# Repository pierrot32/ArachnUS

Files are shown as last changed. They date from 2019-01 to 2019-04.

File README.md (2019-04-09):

# ArachnUS
Projet de conception d'un robot araignée à 3 pattes.

## Mécanique du robot:
Fichier RobotCAD contient toutes les informations pour imprimer ou modifier les pièces du robot avec le logiciel Solidworks.
Plus d'informations sont données dans le fichier.

## Carte openCR
Voir le dossier Code/OpenCr pour la procédure d'installation et d'utilisation de code du robot

## Autres Cartes 
### Utilisation de la carte PCA9685 (branchements sur la carte openCr)
Voir le dossier Documentation électronique

### Uilisation du capteur de distance
Voir le dossier Documentation électronique

## Interface:
Voir le dossier Code/python pour la procédure d'installation et d'utilisation de l'interface pour le contrôle du robot.

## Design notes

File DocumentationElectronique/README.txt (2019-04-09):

Ici sont réunies les premier codes de tests et les informations sur le hardware que nous avons utilisé.

Ci-dessous une liste de références pour l'électronique du robot:

Guide d'utilisation du contrôleur PCA9685:
https://learn.adafruit.com/16-channel-pwm-servo-driver/overview

Guide d'utilisateur de la carte OpenCR:
http://emanual.robotis.com/docs/en/parts/controller/opencr10/
http://support.robotis.com/en/product/controller/opencr.htm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

Fiches techniques :
Moteur MG996R : http://magicduino.com/Images/ItemsMedia/File/7203.pdf
Capteur de hauteur HC-SR04 :
La section utile au capteur est le chapitre 24 du tutoriel, c'est dans cette section que le code utilisé a été pris.
Cette section contient aussi les informations sur l'alimentation électrique du capteur.
https://github.com/Freenove/Freenove_Ultimate_Starter_Kit_for_Arduino/blob/master/Tutorial.pdf

Pour l'installation de la carte OpenCR sur arduinoIDE (sur Windows): 
1) Fichier -> préférence -> URL de gestionnaire des cartes suppl. -> https://raw.githubusercontent.com/ROBOTIS-GIT/OpenCR/master/arduino/opencr_release/package_opencr_index.json
2) Tools -> board -> board manager -> "opencr" dans la barre de recherche -> install
3) Tools -> board -> "OpenCR Board"
4) Tools -> port -> COMX (*une fois connecte)

Pour MAC ou autre, voir le guide d'utilisateur de la carte OpenCR^^

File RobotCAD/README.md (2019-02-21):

# RobotCAD
Ce fichier contient tous les dessins 3D pour construire le robot, ainsi que les informations pour le fabriquer

## Pieces à imprimer:
Fichier contenant les fichier STL et STEP des pieces à imprimer. Voir le README de ce fichier pour avoir les quantitées exact de pièces à imprimer

## Base/Pattes:
Pieces SLDPRT utilisées pour concevoir le robot

## Assemblage:
Assemblages du robot et document sur comment assembler le robot.

## Cartes/ServoMoteurs:
Dessins 3D des cartes et des servo moteurs du robot

## Dev:
Fichier contenant les pièces de développement utilisés dans la conception du robot

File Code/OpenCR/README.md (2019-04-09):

##  Guide d'utilisateur de la carte OpenCR:
http://emanual.robotis.com/docs/en/parts/controller/opencr10/
http://support.robotis.com/en/product/controller/opencr.htm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

## OpenCR et PCA9685:
Pour utiliser la carte OpenCR dans notre appliquation, il faut:
1. Télécharger arduinoIDE
2. Télécharger la carte "OpenCR" dans arduinoIDE 
  a) Fichier -> préférence -> URL de gestionnaire des cartes suppl. -> https://raw.githubusercontent.com/ROBOTIS-GIT/OpenCR/master/arduino/opencr_release/package_opencr_index.json
  b) Tools -> board -> board manager -> "opencr" dans la barre de recherche -> install
  c) Tools -> board -> "OpenCR Board"
  d) Tools -> port -> COMX (*une fois connecte)
3. Télécharger la librairie "adafruit servo" dans arduinoIDE
4. Assembler la carte PCA9685 (https://learn.adafruit.com/16-channel-pwm-servo-driver/assembly)
5. Faire les connections électriques entre le PCA9685, le OpenCR et les servos moteur (https://learn.adafruit.com/16-channel-pwm-servo-driver/hooking-it-up)
6. Connecter l'alimentation externe
7. Connecter la prise USB et téléverser le programme "Programme principal"

*NOTE*: Toujours brancher l'alimentation externe avant de brancher le cable USB

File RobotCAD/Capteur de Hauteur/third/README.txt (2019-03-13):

the source of the files contained in this directory is: https://grabcad.com/library/ultrasonic-distance-measuring-sensor-module-for-arduino-1

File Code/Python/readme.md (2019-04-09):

## Installation de python
1.  Télécharger python 3.7
2.  Télécharger Pycharm (ou autre environnement de programmation en python)
3.  Ajouter les librairies suivantes: pip (19.0.1), numpy (1.16.1), pyserial (3.4) et matplotlib (3.0.3)

## Ajustement du code pour utilisation de la communication en l'ordinateur et la carte oprenCR
1.  Veuillez vérifier que le code utilise le bon port USB de votre ordinateur ('COM3')
    a)  Ouvrir arduinoIDE
    b)  Brancher la carte openCR
    c)  Outil(barre de menu) -> port -> Noter le port
2. Ajuster le code de communication
  a)  Ouvrir le fichier communication.py à l'aide de pycharm
  b)  Voir ligne 119
  c)  Changer COM3 par le port utilisé par votre ordinateur
    
##  Utilisation de l'interface
1.  Ouvrir le fichier Main.py
2.  S'assurer que la carte openCR est branché sur l'ordinateur
3.  Exécuter le code
4.  Le robot démarre en mode arrêt
5.  Changer le mode à manuel pour le contrôle individuel de chaque moteur
6.  ...

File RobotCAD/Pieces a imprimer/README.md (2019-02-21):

# Pieces à imprimer:

Voici la liste des pieces à imprimer et leur quantitée

Barre_Bleu1           -> x3

Barre_Bleu2           -> x3

Barre_Bleu3           -> x3

Barre_Rouge1          -> x3
 
Barre_Rouge2          -> x3
 
Barre_Rouge3          -> x3
 
Barre_Vert            -> x3
 
Base_Moteur           -> x3
 
Espaceur_Plaques      -> x4
 
Joint_RB              -> x3
 
Pied_de_patte         -> x3
 
Plaque_Bas            -> x1
 
Plaque_Top            -> x1
 
Porteur_moteur        -> x2

Protecteur_de_Cartes  -> x1
 
Support_de_Cartes     -> x1

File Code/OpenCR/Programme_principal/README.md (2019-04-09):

## Utilisation du programme de contrôle du robot
  Pour utiliser ce programme, il faut préalablement avoir réaliser les étapes pour avoir accès à l'interface.
  
  1. Ouvir le programme principal
  2. Téléverser le programme vers la carte openCR
  3. Lancer l'interface
  4. Utiliser l'interface pour contrôler les différents modes du robot

## Ajustement du range des pattes du robots
  
  1. Ouvrir le code fonctionsServos
  2. Faire monter le robot le plus haut possible à l'aide de l'interface
  3. Changer les ranges dans le code pour s'assurer de respecter les limites de la pattes

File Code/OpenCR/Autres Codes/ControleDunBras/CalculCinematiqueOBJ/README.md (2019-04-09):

Ici a été développé la classe -> ObjCinematique.h

Une fois inclue dans un code elle, permet de faire la cinématique directe et inverse de notre systeme.

Cette classe utilise la librairie "matrix", concue par François Grondin,
dans laquel nous avons ajouté quelques fonctionnalités.

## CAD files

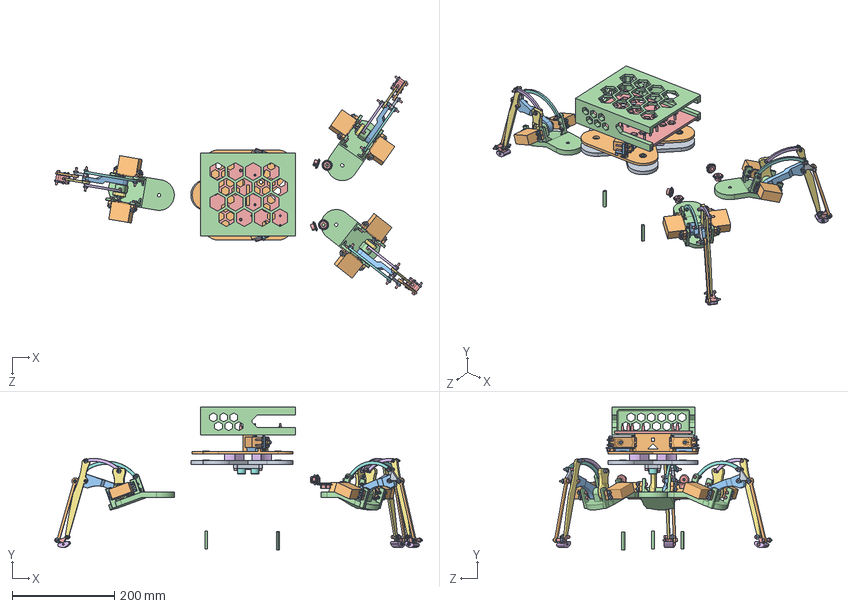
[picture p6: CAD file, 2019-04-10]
RobotCAD/Assemblages/Tripod.SLDASM
720.4 x 279.4 x 428.7 mm
Plaque_Bas
Plaque_Top
Porteur_moteur x 2
Protecteur_de_Cartes
Support_de_Cartes
Espaceur_Plaques x 4
bearing_2 x 6
hc-sr04
Support_Capteur
servo x 8
shaft x 8
Washer_plas x 16
socket head cap screw_ai x 64
Barre_Bleu2 x 3
Barre_Bleu3 x 3
Barre_Rouge1 x 3
Barre_Rouge2 x 3
Barre_Rouge3 x 3
Barre_Vert x 3
Base_moteurs x 3
Joint_RB x 3
Pied_de_patte x 3
Barre_Bleu1 x 3
Washer_1 x 30
bearing_1 x 6
Spacer pour servo moteur_1 x 24
machine screw nut hex_ai x 56
Shaft_1 x 3
615398.STEP x 4
632134_91375A436.STEP x 4

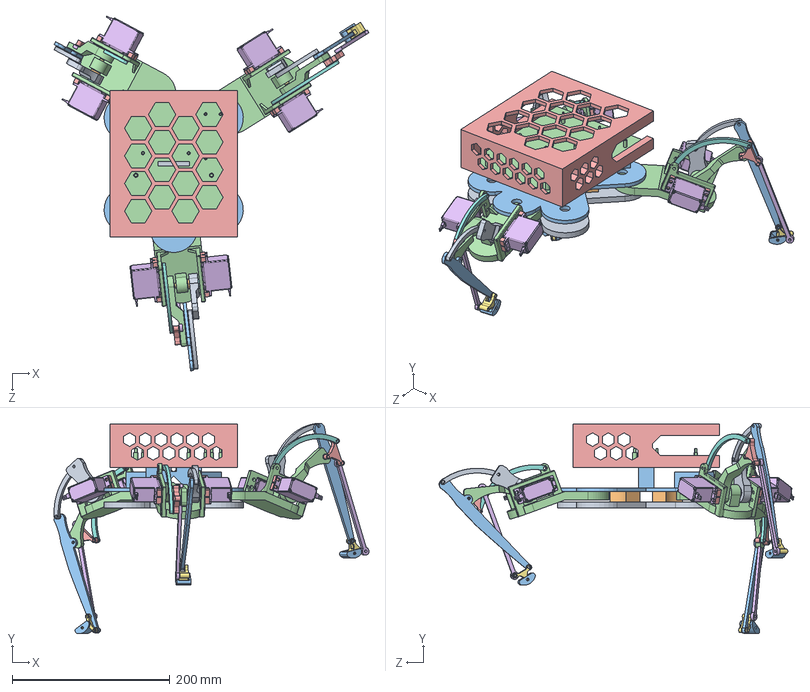
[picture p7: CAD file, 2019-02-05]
RobotCAD/Dev/Assemblage_du_robot.SLDASM
399.4 x 266.8 x 449.9 mm
base_v3-bas
SpacerCarteDuBas x 4
base_v3-top
Base x 3
Spacer pour servo moteur x 24
hs-422_sws x 6
shaft-18 x 3
Connecteur_servo_moteur x 6
Bleu1 x 3
bearing x 6
Bleu3 x 3
Vert x 3
Rouge2 x 3
Rouge3 x 3
Joint R-B x 3
Rouge1 x 3
Bleu2.0 x 3
WASHER x 36
Pied de patte x 3
support_carte
cover carte

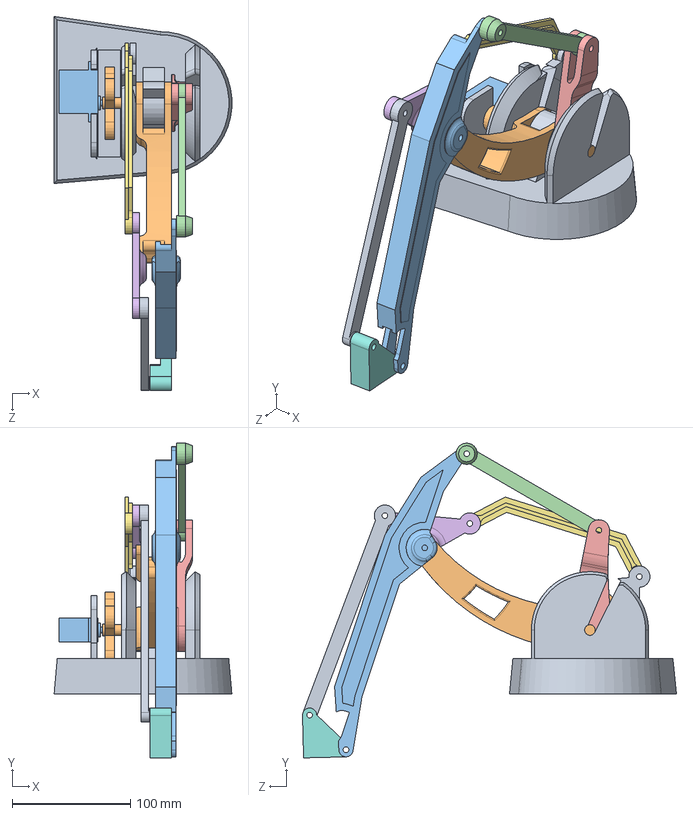
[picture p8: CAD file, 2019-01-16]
RobotCAD/Dev/Robot_fait_pour_projet_S1/Robotic Arm/Robotic.SLDASM
150.1 x 265.8 x 315.7 mm
Boutte_Servo
Modèle_servomoteur

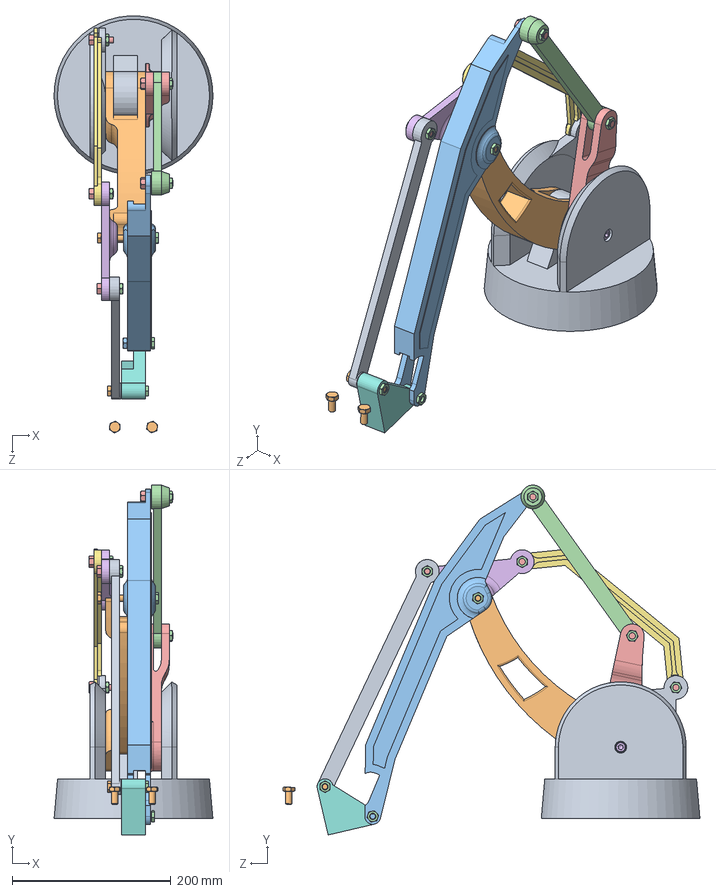
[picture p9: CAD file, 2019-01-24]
RobotCAD/Dev/Robot_ordinaire_download/Robotic Arm/Robotic.SLDASM
199.9 x 440.4 x 524.8 mm
hex cap screw_am x 4
formed hex screw_am
hex nut jam_am x 9
hex screw_am x 5
socket head cap screw_am

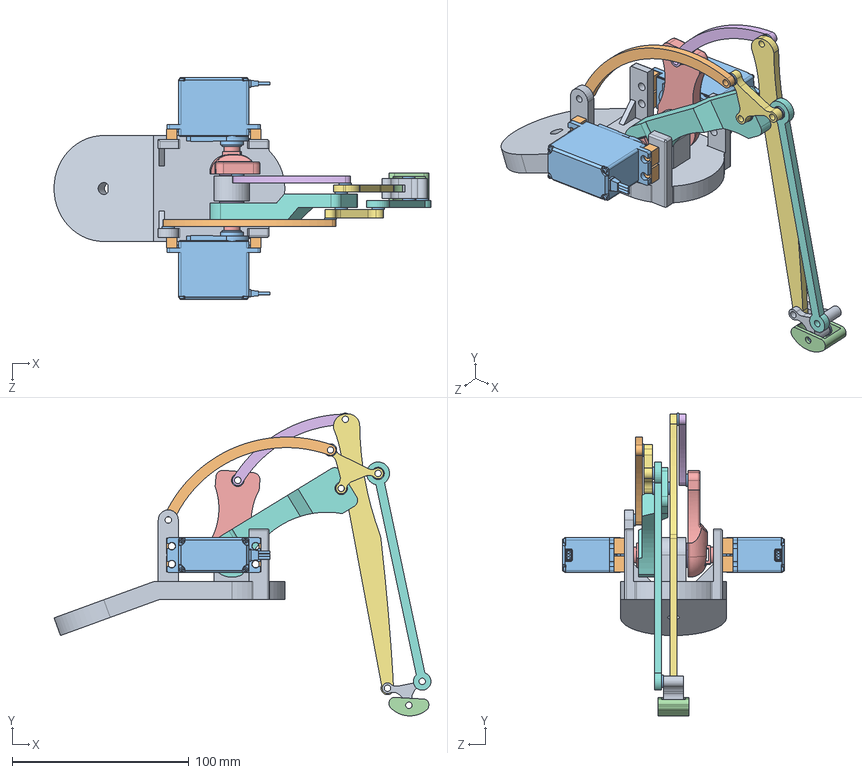
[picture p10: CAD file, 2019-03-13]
RobotCAD/Dev/Robot_v1_POL/Assemblage1.SLDASM
213.4 x 171.4 x 125.6 mm
Base2
Spacer pour servo moteur x 8
hs-422_sws x 2
shaft-18
Connecteur_servo_moteur x 2
bearing x 2
Bleu3
Vert
Joint R-B
Rouge1
WASHER x 10
Pied de patte
Bleu1
Bleu2.0
Rouge2
Rouge3

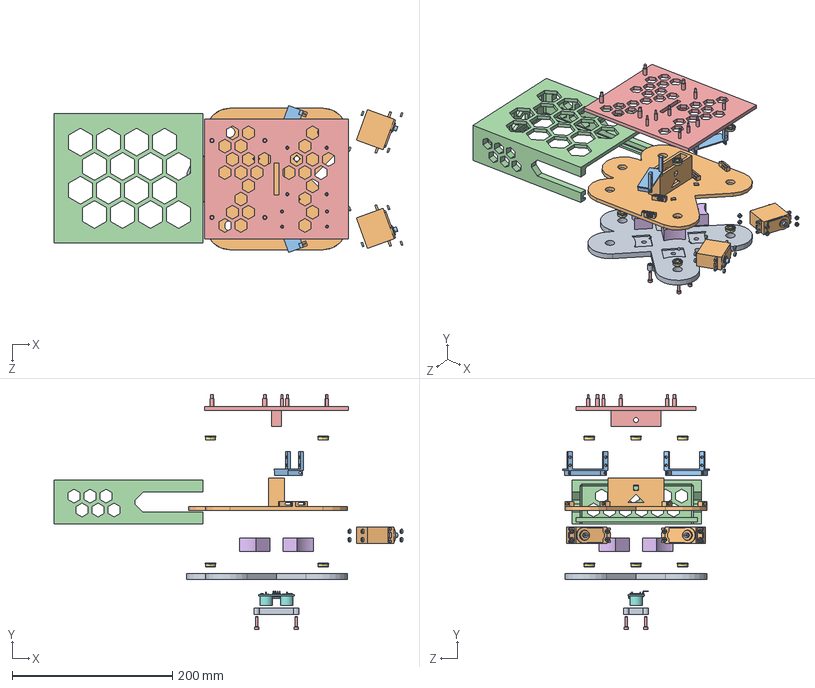
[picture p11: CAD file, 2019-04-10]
RobotCAD/Assemblages/Base.SLDASM
435.4 x 293.5 x 183.2 mm
Plaque_Bas
Plaque_Top
Porteur_moteur x 2
Protecteur_de_Cartes
Support_de_Cartes
Espaceur_Plaques x 4
bearing_2 x 6
hc-sr04
Support_Capteur
servo x 2
shaft x 2
Washer_plas x 16
socket head cap screw_ai x 4

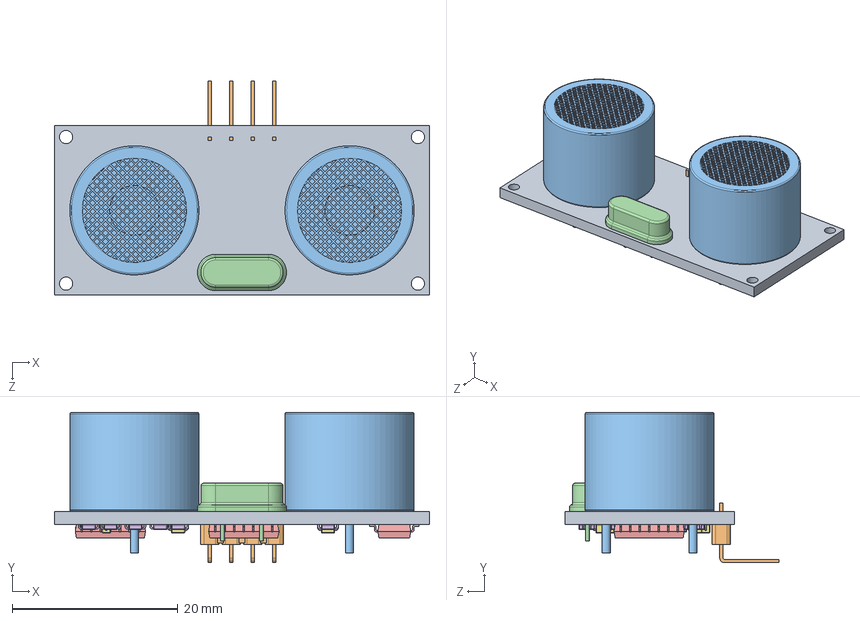
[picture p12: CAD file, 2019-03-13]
RobotCAD/Capteur de Hauteur/hc-sr04.SLDASM
45.3 x 18.2 x 25.9 mm
pcb
connector
speaker x 2
osilator
microprocessor_1 x 3
resistor x 14
Capacitor x 7

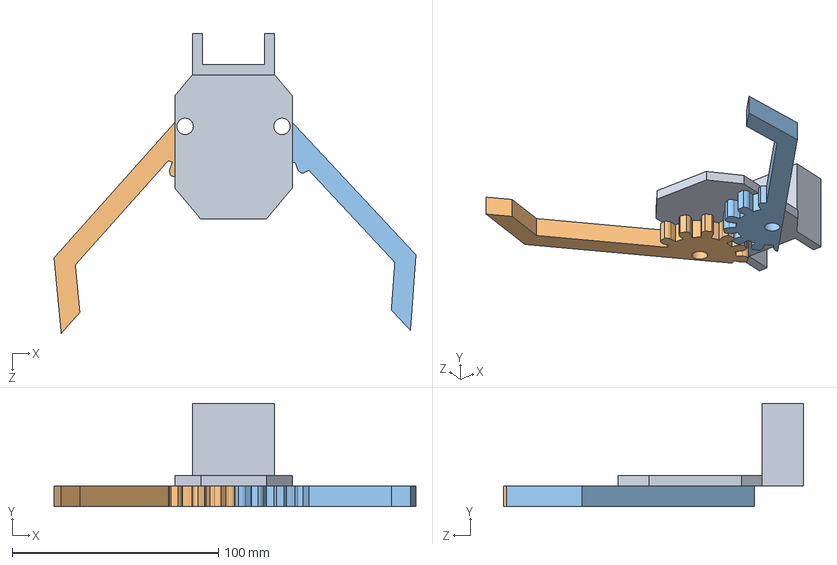
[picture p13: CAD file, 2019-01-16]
RobotCAD/Dev/Robot_fait_pour_projet_S1/Robotic Arm/Assem2.SLDASM
175.7 x 50.0 x 145.5 mm

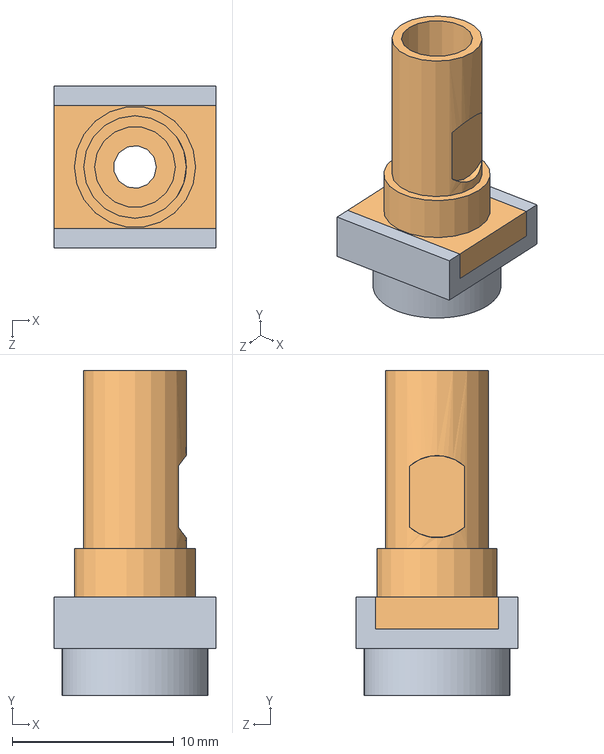
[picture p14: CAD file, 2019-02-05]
RobotCAD/ServoMoteur/connecteur_servo_engr_assemble.SLDASM
10.0 x 20.1 x 10.0 mm
Connecteur_servo_moteur
connecteur_servo_engrenage

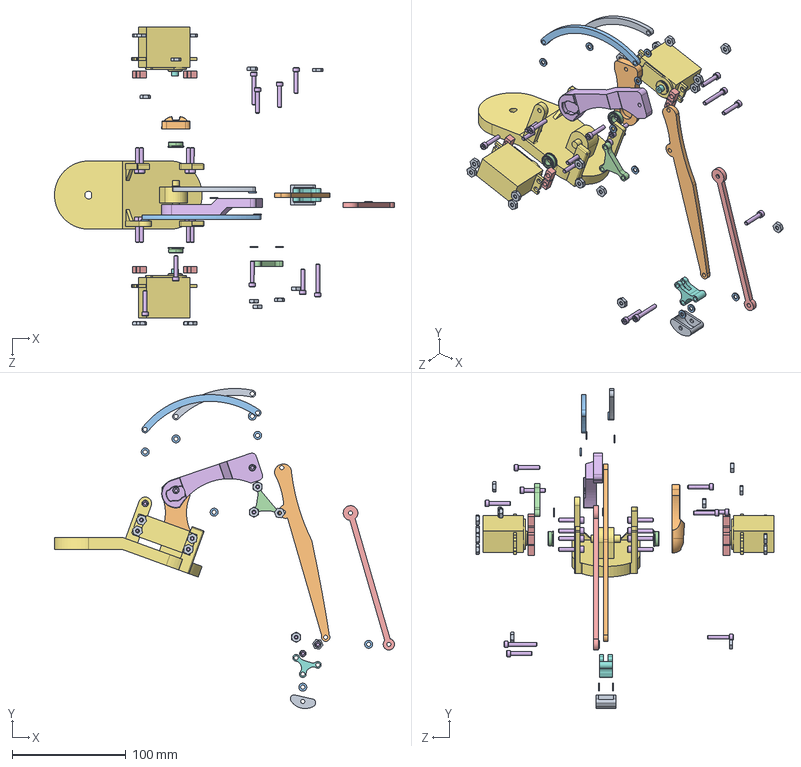
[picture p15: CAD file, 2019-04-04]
RobotCAD/Assemblages/Patte.SLDASM
299.1 x 281.5 x 262.0 mm
Barre_Bleu2
Barre_Bleu3
Barre_Rouge1
Barre_Rouge2
Barre_Rouge3
Barre_Vert
Base_moteurs
Joint_RB
Pied_de_patte
Barre_Bleu1
Washer_1 x 10
bearing_1 x 2
Spacer pour servo moteur_1 x 8
socket head cap screw_ai x 17
servo x 2
shaft x 2
machine screw nut hex_ai x 16

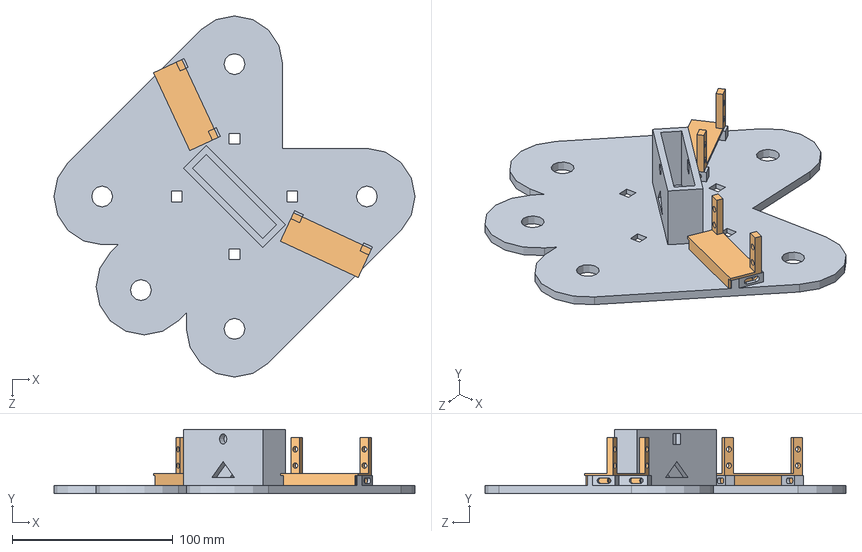
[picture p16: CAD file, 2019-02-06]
RobotCAD/Dev/base/assemblage_base_top_glissiere.SLDASM
224.9 x 40.0 x 224.9 mm
base_v3-top-glissiere
glissiere_connexion_moteur x 2

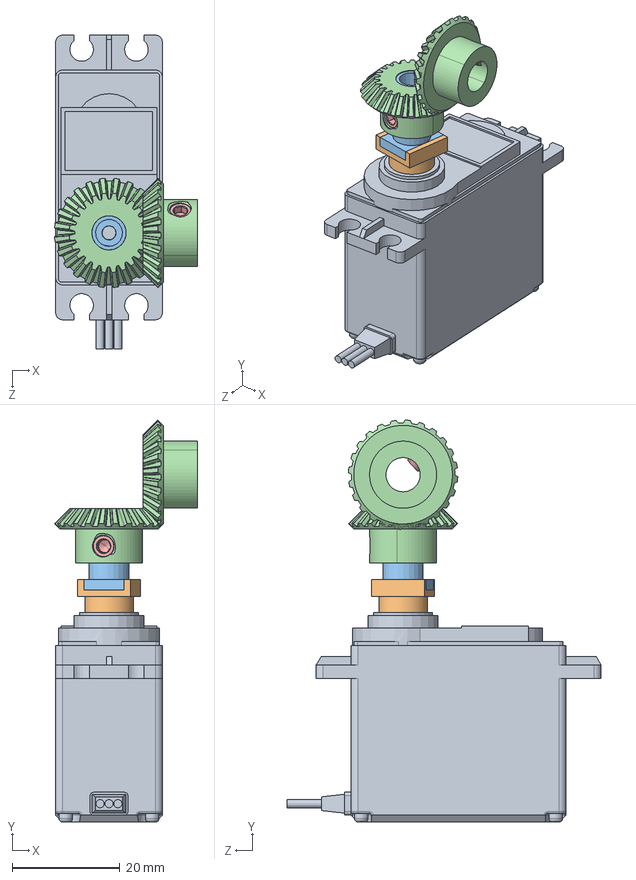
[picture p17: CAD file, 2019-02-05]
RobotCAD/ServoMoteur/assemblage_servo_engrenage.SLDASM
26.6 x 74.6 x 58.2 mm
hs-422_sws
Connecteur_servo_moteur
connecteur_servo_engrenage
615398.STEP x 2
632134_91375A436.STEP x 2

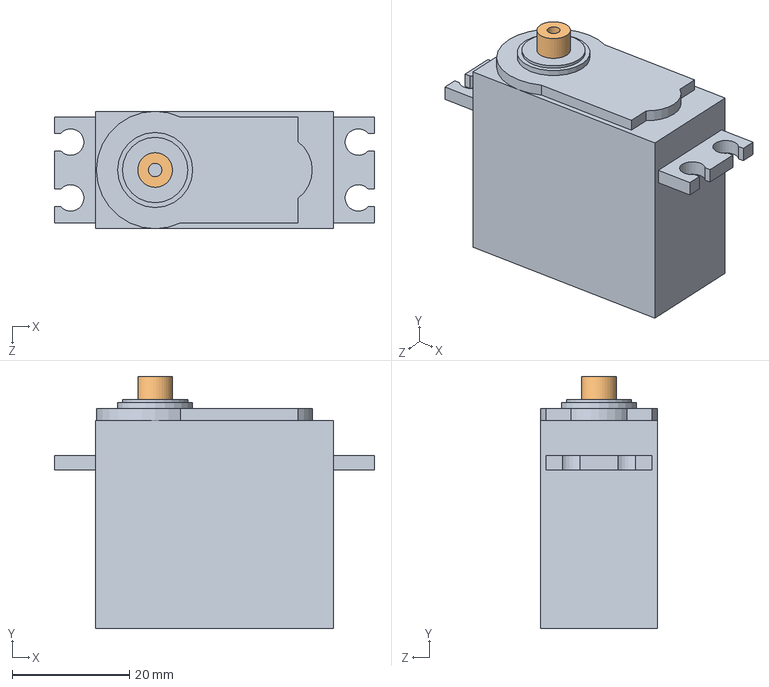
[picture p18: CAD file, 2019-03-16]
RobotCAD/ServoMoteur/MG996R/MG996R.SLDASM
54.5 x 43.0 x 20.0 mm
servo
shaft

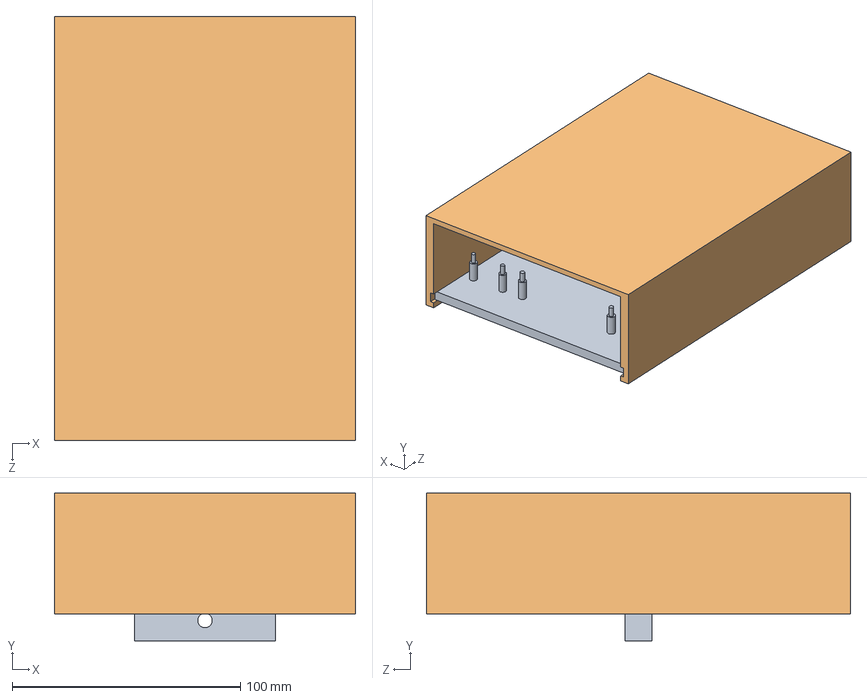
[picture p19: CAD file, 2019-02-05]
RobotCAD/Dev/base/assemblage_support_carte_et_cover.SLDASM
132.0 x 64.9 x 186.0 mm
support_carte
cover carte

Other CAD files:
RobotCAD/ServoMoteur/assemblage_servo_engrenage_2e_cote.SLDASM
RobotCAD/Dev/base/assemblage_base_support_carte.SLDASM
RobotCAD/Dev/base/assemblage_base_top.SLDASM
RobotCAD/base/Assemblage_de_la_base.SLDASM
RobotCAD/Assemblages/Patte.SLDDRW
RobotCAD/Base/Espaceur_Plaques.SLDPRT
RobotCAD/Base/Plaque_Bas.SLDPRT
RobotCAD/Base/Plaque_Top.SLDPRT
RobotCAD/Base/Porteur_moteur.SLDPRT
RobotCAD/Base/Protecteur_de_Cartes.SLDPRT
RobotCAD/Base/Support_de_Cartes.SLDPRT
RobotCAD/Capteur de Hauteur/Support_Capteur.SLDPRT
RobotCAD/Capteur de Hauteur/hc-sr04.SLDPRT
RobotCAD/Capteur de Hauteur/osilator.SLDPRT
RobotCAD/Capteur de Hauteur/pcb.SLDPRT
RobotCAD/Capteur de Hauteur/third/microprocessor_1.sldprt
RobotCAD/Capteur de Hauteur/third/resistor.sldprt
RobotCAD/Capteur de Hauteur/third/speaker.sldprt
RobotCAD/Cartes/16-channel-pca9685-1/PCA9685.SLDPRT
RobotCAD/Cartes/OpenC_dimensions.SLDPRT
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

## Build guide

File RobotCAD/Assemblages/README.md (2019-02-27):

# Arachnus
Projet de conception d'un robot araignée à 3 pattes.

## Assemblage

Pour assembler notre robot, il faut imprimer toutes les pièces nécessaires pour le robot qui sont dans le dossier "Pièces à imprimer" (https://github.com/pierrot32/ArachnUS/tree/master/RobotCAD/Pieces%20a%20imprimer).

Assembler chacune des pattes du robot en se basant sur le modèle 3D et en suivant ces recommendations :
1. Utiliser des boulons 6-32 3/4" pour assembler le robot, sauf pour la jonction entre les pièces bleu3, rouge2 et verte où un boulon de 1" est requis.
2. Utiliser des écrous autobloquant pour éviter qu'ils ne se desserrent durant l'utilisation du robot.
3. Placer une rondelle entre chaque pièce de plastique pour éviter le frottement plastique/plastique
4. Placer les moteurs en dernier et utiliser les séparateurs de caoutchouc pour qu'ils soient bien alligner avec l'arbre de rotation
5. S'assurer que chaque moteur peut atteindre les 2 maximums de leur axe de rotation

Assembler le robot en se basant sur le modèle 3D de l'assemblage complet et en suivant ces recommendations :
1. Utiliser des boulons 1/4-20 de 1 1/4"
2. Faire passer les câbles des différents moteurs dans la cavité centrale avant de placer le support à cartes

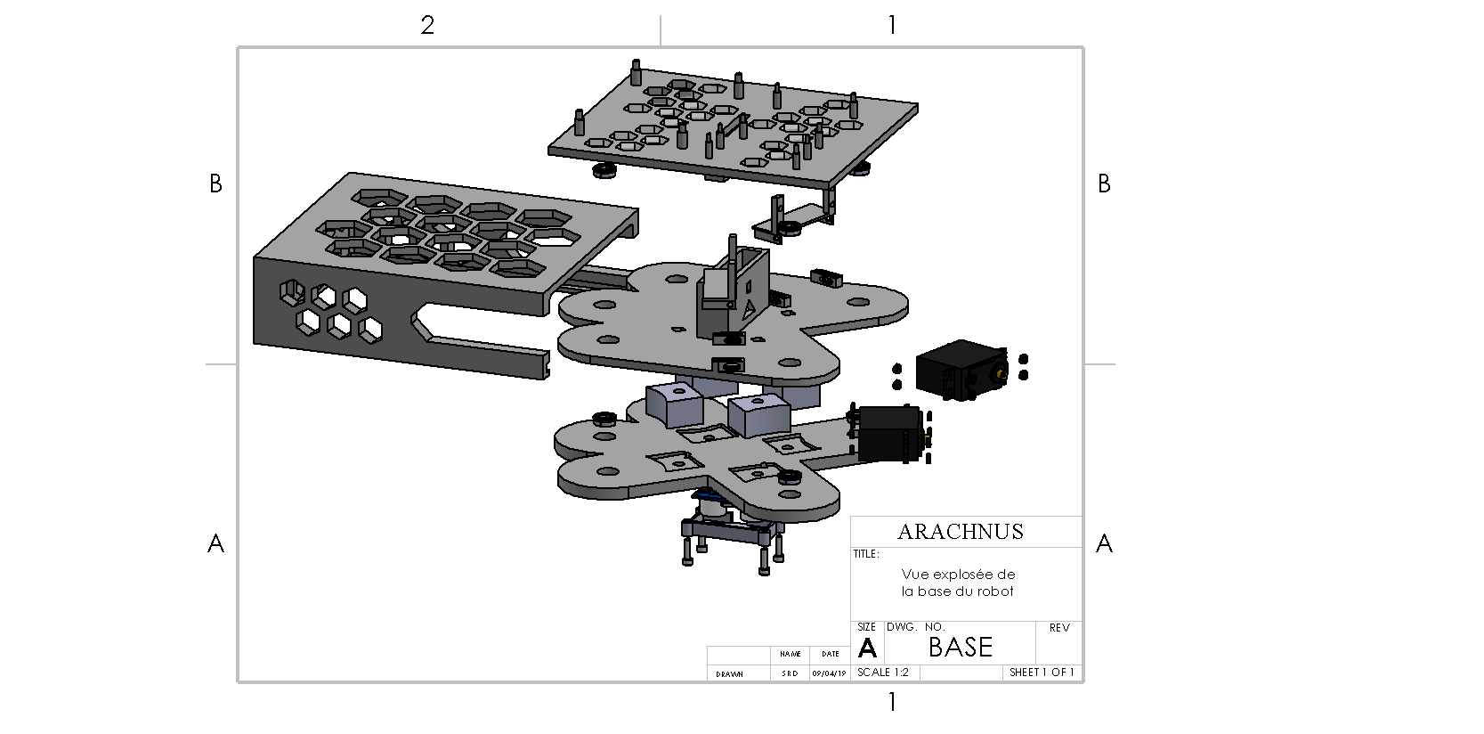
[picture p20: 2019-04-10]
RobotCAD/Assemblages/Base_eplode.PNG

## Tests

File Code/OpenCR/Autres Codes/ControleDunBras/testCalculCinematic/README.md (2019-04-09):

Les premières ébauches de calcules de cinématique embarquée on été réalisé ici.

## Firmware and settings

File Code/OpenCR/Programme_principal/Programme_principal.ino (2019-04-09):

/*
 * Le programme ci-dessous à été réalisé par l'équipe d'ARACHNUS
 * dans la cadre d'un cours de projet en génie robotique
 * de l'université de Sherbrooke (S4-GRO).
 */


/*************************************************** 
  Programme principal pour le contrôle du robot
 ****************************************************/

#include <IMU.h>                                    // Librairie pour l'utilisation de l'accéléromètre

#define NBR_DE_SERVO 8                              // Nombre de servo moteur utilisé pour le robot

cIMU    IMU;                                        // Objet pour utilisation de l'acéléromètre

int initDone = 0;                                   // Variable pour savoir si l'initialisation est fait

//*****CONSTANTES ET VARIABLES POUR FILTRE DES MOTEURS*****//
#define coeffFiltre 7                               // Nombre de coefficient utilisé pour le filtre FIR à moyenne mobile
float filtreMot1[coeffFiltre];                      // Les entrée du filtre à moyenne mobile pour le moteur côté vert de la patte 1
float filtreMot2[coeffFiltre];                      // Les entrée du filtre à moyenne mobile pour le moteur côté vert de la patte 2
float filtreMot3[coeffFiltre];                      // Les entrée du filtre à moyenne mobile pour le moteur côté vert de la patte 3
int indexCirculaire = 0;                            // Index pour entrée les angles calculé dans la bonne case du tableau des filtres des différents moteurs

int moyenneFiltreMoteur1 = 0;                       // Moyenne mobile calculé pour le moteur côté vert de la patte 1
int moyenneFiltreMoteur2 = 0;                       // Moyenne mobile calculé pour le moteur côté vert de la patte 2
int moyenneFiltreMoteur3 = 0;                       // Moyenne mobile calculé pour le moteur côté vert de la patte 3


//*****STRUCTURE POUR COMMUNICATION ENTRE OPENCR ET ORDINATEUR PAR PORT SERIAL*****//
// La structure envoi est celle utilisé pour la communication par le port serial vers l'ordinateur
typedef struct envoi{
  long etat;
  long moteur0;                                     // Angle présente du moteur côté bleu de la patte 1
  long moteur1;                                     // Angle présente du moteur côté vert de la patte 1
  long moteur2;                                     // Angle présente du moteur côté bleu de la patte 2
  long moteur3;                                     // Angle présente du moteur côté vert de la patte 2
  long moteur4;                                     // Angle présente du moteur de sélection de l'angle de la patte 1
  long moteur5;                                     // Angle présente du moteur de sélection de l'angle de la patte 2
  long moteur6;                                     // Angle présente du moteur côté bleu de la patte 3
  long moteur7;                                     // Angle présente du moteur côté vert de la patte 3
  long hauteur;                                     // Hauteur entre le sol et le robot trouver à l'aide du capteur de hauteur
  long angx;                                        // Angle x du robot
  long angy;                                        // Angle y du robot
};
envoi msg_Envoi;                                    // Objet pour le message d'envoi vers le robt

//*****VARIABLES POUR LE CALCUL DE LA HAUTEURS DU ROBOT*****//
int delta_hauteur;                                  // Le changement de hauteur du robot pour atteindre celle désirée
int hauteur_actuelle;                               // Hauteur actuelle trouvé avec le capteur de hauteur




//*****VARIABLES POUR RECEVOIR LA STRUCUTRE DE COMMUNICATION*****//
byte buff[10*sizeof(long)];                         // Grandeur de la structure reçu lors de la communication avec l'ordinateur
int state[NBR_DE_SERVO];                            // État voulue (Sélectionné par l'interface lors de la communication) (Doit être dans un tableau pour le bon fonctionnement par communication par structure)
int height[NBR_DE_SERVO];                           // Hauteur voulue (Sélectionné par l'interface lors de la communication) (Doit être dans un tableau pour le bon fonctionnement par communication par structure)
int valeurs_Angles_moteurs[NBR_DE_SERVO];           // Valeur d'angle au moteur pour initialisation, état manuel et lors du calcul de stabilisation


//*****STRUCUTURE POUR LE CALCUL D'ANGLE DU ROBOT*****//
typedef struct angleRobot{
  float angleX = 0.0;                               // Angle en x du robot
  float angleY = 0.0;                               // Angle en y du robot
};
angleRobot aRobot;                                  // Objet utilisé pour le calcul de l'angle du robot

//*****PIN POUR LE CAPTEUR DE HAUTEUR*****//
uint8_t   trigPin = 12;
uint8_t   echoPin = 11;

//*****VARIABLES DE TEMPS*****//
static uint32_t tTime[3];                           // Tableau qui contient différents temps calculé
static uint32_t imu_time = 0;                       // Temps de la dernière fois que l'accéléromètre à été utilisé

//*****VARIABLE POUR LE CALCUL DU CHANGENT D'ANGLE POUR LA STABILISATION DU ROBOT*****//
typedef struct deltaAngleMoteurHauteur{
  float deltaAngleMoteur1 = 0;                      // Changment d'angle du moteur côté vert de la patte 1
  float deltaAngleMoteur2 = 0;                      // Changment d'angle du moteur côté vert de la patte 2
  float deltaAngleMoteur3 = 0;                      // Changment d'angle du moteur côté vert de la patte 3 
};
deltaAngleMoteurHauteur dMAngle;                    // Objet pou rle calcul lors de la stabilisation

void envoi_serie(envoi MSG, int valeurs_moteurs[NBR_DE_SERVO]);

//*****SETUP DU RU PROGRAMME*****//
void setup() {
  Serial.begin(115200);
  IMU.begin();
  pinMode(trigPin,OUTPUT);// set trigPin to output mode   
  pinMode(echoPin,INPUT); // set echoPin to input mode
  initFctServo(valeurs_Angles_moteurs);
  for (int i=0;i<coeffFiltre;i++){
    filtreMot1[i] = 0;
    filtreMot2[i] = 0;
    filtreMot3[i] = 0;
  }
  
}





//*****LOOP DU PROGRAMME*****/
void loop() {
  //Boucle de communication//
  // La carte fait la lecture du port sérial tant que des structures son disponible
  while(Serial.available() > 0){
    if(lecture(buff)){
      copie_array_struc(buff,valeurs_Angles_moteurs, state, height);
    }
  }

  //Machine à état fini pour sélection de l'état du robot
  switch(state[0]){
    
    //État d'arrêt//
    case 0:
      // Rien ne se produit dans cet état
      initDone = 0;
      break;

    //État d'initialisation//
    case 1:
      // Rien ne se produit pour l'instant dans cet état.
      msg_Envoi.etat = 1;
      initDone = 1;
      break;

    //État manuel//
    case 2:
      // Contrôle des moteurs à l'aide de l'interface
      msg_Envoi.etat = 2;
      updateServos(valeurs_Angles_moteurs);
        break;        

    //État de stabilisation//
    case 3:
      // Stabilisation automatique du robot (n'inclus pas la cinématique inverse dans cette version)
      msg_Envoi.etat = 3;

        // Calcul de l'angle du robot
        aRobot = calculAngle(IMU.accRaw[0],IMU.accRaw[1], IMU.accRaw[2]);

        // Calcul des variations d'angle des trois moteur de position en y du robot
        dMAngle = stabilisationRobot(aRobot);

        // Mise à jour de la hauteur actuelle du robot
        hauteur_actuelle = int(getSonar());

        // Ajout des nouvelle valeurs calculé au filtre (avec varition de hauteurs)
        filtreMot1[indexCirculaire] = dMAngle.deltaAngleMoteur1 + (height[0]-hauteur_actuelle);
        filtreMot2[indexCirculaire] = dMAngle.deltaAngleMoteur2 + (height[0]-hauteur_actuelle);
        filtreMot3[indexCirculaire] = dMAngle.deltaAngleMoteur3 + (height[0]-hauteur_actuelle);

        // Mise à jour de l'index pour l'ajout des données aux filtres des moteurs
        if (indexCirculaire>=coeffFiltre){
          indexCirculaire++;
        } else {
          indexCirculaire = 0;
        }

        // Calcul de la moyenne mobile des moteurs
        moyenneFiltreMoteur1 = filtreMoyenneMobile(filtreMot1, coeffFiltre);
        moyenneFiltreMoteur2 = filtreMoyenneMobile(filtreMot2, coeffFiltre);
        moyenneFiltreMoteur3 = filtreMoyenneMobile(filtreMot3, coeffFiltre);
        
        // Limites de chaque moteurs
        if( valeurs_Angles_moteurs[7] + moyenneFiltreMoteur1>=0 && valeurs_Angles_moteurs[7] + moyenneFiltreMoteur1<= 90){
          valeurs_Angles_moteurs[7] = valeurs_Angles_moteurs[7] + moyenneFiltreMoteur1;
        }
        if( valeurs_Angles_moteurs[3]+ moyenneFiltreMoteur2>=0 && valeurs_Angles_moteurs[3]+ moyenneFiltreMoteur2<= 90){
          valeurs_Angles_moteurs[3] = valeurs_Angles_moteurs[3] + moyenneFiltreMoteur2;
        }
        if( valeurs_Angles_moteurs[1]+ moyenneFiltreMoteur3>=0 && valeurs_Angles_moteurs[1]+ moyenneFiltreMoteur3<= 90){
          valeurs_Angles_moteurs[1] = valeurs_Angles_moteurs[1] + moyenneFiltreMoteur3;
        } 
               
        // Update des servos moteurs
        updateServos(valeurs_Angles_moteurs);

      break;

  }

  // Envois des données vers l'interface à chaque 100 ms
  if( (millis()-tTime[1]) >= 100 ){
    tTime[1] = millis();
    envoi_serie(msg_Envoi,valeurs_Angles_moteurs);
  }

  // Délais de 20 ms entre chaque loop
  delay(50);
}

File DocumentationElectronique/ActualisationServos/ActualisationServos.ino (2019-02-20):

/*************************************************** 
  Actualisation de l'ensemble des servos
 ****************************************************/
 
#include <Wire.h>
#include <Adafruit_PWMServoDriver.h>

// L'adresse de la carte PCA9685 est 0x41.
Adafruit_PWMServoDriver pwm = Adafruit_PWMServoDriver(0x41);

//À valider:
#define SERVOMIN  200 // this is the 'minimum' pulse length count (out of 4096)
#define SERVOMAX  450 // this is the 'maximum' pulse length count (out of 4096)
#define ANGLEMIN  0
#define ANGlEMAX  145
#define NBR_DE_SERVO 8

// Compteur de servo
int numServo = NBR_DE_SERVO;
int angleVoulu = 0;
String commande = String(NULL);
int valeurMoy = ((SERVOMAX-SERVOMIN)/2)+SERVOMIN;
int valeursAngle[NBR_DE_SERVO];


// Convertie une consigne d'angle au moteur en une longueur de pulse pour le pwm
int angleAPulse(int angle) {
  if(angle<ANGLEMIN){
    angle = ANGLEMIN;
  } else if (angle>ANGlEMAX) {
    angle = ANGlEMAX;
  }
  return map(angle, ANGLEMIN, ANGlEMAX, SERVOMIN, SERVOMAX);
}

// Convertie une consigne de pulse au moteur en une valeur d'angle
int pulseAAngle(int pulse) {
  if(pulse<SERVOMIN){
    pulse = SERVOMIN;
  } else if (pulse>SERVOMAX){
    pulse = SERVOMAX;
  }
  return map(pulse, SERVOMIN, SERVOMAX, ANGLEMIN, ANGlEMAX);
}

// Actualise l'ensemble des servos un après l'autre
void updateServos(int angleVoulu[NBR_DE_SERVO]) {
  for (int i=0; i<NBR_DE_SERVO; i++){
    pwm.setPWM(i, 0, angleAPulse(angleVoulu[i])); 
  }
}


void setup() {
  Serial.begin(9600);

  pwm.begin();
  pwm.setPWMFreq(60);  // Frequence de raffraichissement des servo est ~60 Hz

  for (int i=0; i<NBR_DE_SERVO; i++){
    valeursAngle[i] = pulseAAngle(valeurMoy); 
  }
  updateServos(valeursAngle);
}

void loop() {

  while(Serial.available() > 0){
    numServo = Serial.parseInt();
    angleVoulu = Serial.parseInt();
  }
  valeursAngle[numServo] = angleVoulu;

  Serial.println("------------------------------------------------");
  for(int i=0; i<NBR_DE_SERVO; i++){
    Serial.print("Le moteur #");
    Serial.print(i);
    Serial.print(" est a ");
    Serial.print(valeursAngle[i]);
    Serial.println(" degrees");
  }

  delay(100);   

}

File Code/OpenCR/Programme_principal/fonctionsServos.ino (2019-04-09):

/*
 * Le programme ci-dessous à été réalisé par l'équipe d'ARACHNUS
 * dans la cadre d'un cours de projet en génie robotique
 * de l'université de Sherbrooke (S4-GRO).
 */


/*************************************************** 
  Actualisation de l'ensemble des servos
 ****************************************************/
 
#include <Wire.h>
#include <Adafruit_PWMServoDriver.h>

// L'adresse de la carte PCA9685 est 0x41.
Adafruit_PWMServoDriver pwm = Adafruit_PWMServoDriver(0x41);

//À valider:
#define SERVOMIN  300 // this is the 'minimum' pulse length count (out of 4096)
#define SERVOMAX  450 // this is the 'maximum' pulse length count (out of 4096)
#define ANGLEMIN  0
#define ANGlEMAX  90
#define NBR_DE_SERVO 8

int tabServoMin[NBR_DE_SERVO] = {300,200,320,150,300,300,300,200};
int tabServoMax[NBR_DE_SERVO] = {450,500,450,450,450,450,450,500};
int tabAngleMin[NBR_DE_SERVO] = {0,0,0,0,0,0,0,0};
int tabAngleMax[NBR_DE_SERVO] = {90,90,90,90,90,90,90,90};


// Convertie une consigne d'angle au moteur en une longueur de pulse pour le pwm
int angleAPulse(int angle) {
  if(angle<ANGLEMIN){
    angle = ANGLEMIN;
  } else if (angle>ANGlEMAX) {
    angle = ANGlEMAX;
  }
  return map(angle, ANGLEMIN, ANGlEMAX, SERVOMIN, SERVOMAX);
}

// Convertie une consigne de pulse au moteur en une valeur d'angle
int pulseAAngle(int pulse) {
  if(pulse<SERVOMIN){
    pulse = SERVOMIN;
  } else if (pulse>SERVOMAX){
    pulse = SERVOMAX;
  }
  return map(pulse, SERVOMIN, SERVOMAX, ANGLEMIN, ANGlEMAX);
}

// Actualise l'ensemble des servos un après l'autre
void updateServos(int angleVoulu[NBR_DE_SERVO]) {
    for(int i = 0; i<NBR_DE_SERVO; i++){
      if(angleVoulu[i]<tabAngleMin[i]){
        angleVoulu[i]=tabAngleMin[i];
      } else if(angleVoulu[i]>tabAngleMax[i]){
        angleVoulu[i]=tabAngleMax[i];
      }
    }
    
    pwm.setPWM(0, 0, map(angleVoulu[0], tabAngleMin[0], tabAngleMax[0], tabServoMin[0], tabServoMax[0]));
    pwm.setPWM(1, 0, map(angleVoulu[1], tabAngleMin[1], tabAngleMax[1], tabServoMin[1], tabServoMax[1]));
    pwm.setPWM(2, 0, map(angleVoulu[2], tabAngleMin[2], tabAngleMax[2], tabServoMin[2], tabServoMax[2]));
    pwm.setPWM(3, 0, map(angleVoulu[3], tabAngleMin[3], tabAngleMax[3], tabServoMin[3], tabServoMax[3]));
    pwm.setPWM(4, 0, map(angleVoulu[4], tabAngleMin[4], tabAngleMax[4], tabServoMin[4], tabServoMax[4]));
    pwm.setPWM(5, 0, map(angleVoulu[5], tabAngleMin[5], tabAngleMax[5], tabServoMin[5], tabServoMax[5]));
    pwm.setPWM(6, 0, map(angleVoulu[6], tabAngleMin[6], tabAngleMax[6], tabServoMin[6], tabServoMax[6]));
    pwm.setPWM(7, 0, map(angleVoulu[7], tabAngleMin[7], tabAngleMax[7], tabServoMin[7], tabServoMax[7]));
}

void initFctServo(int valeursAngle[]) {

  pwm.begin();
  pwm.setPWMFreq(60);  // Frequence de raffraichissement des servo est ~60 Hz

  int valeurMoy = ((SERVOMAX-SERVOMIN)/2)+SERVOMIN;


  for (int i=0; i<NBR_DE_SERVO; i++){
    valeursAngle[i] = pulseAAngle(valeurMoy); 
  }
  valeursAngle[0] = 80;
  valeursAngle[2] = 80;
  valeursAngle[6] = 80;
  updateServos(valeursAngle);
}

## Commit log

2019-01-15 Robot Cad Folder + Servo S3 Cad
    Addition of the Robot Cad Folder containning the 3D models of the servo motors that we will use
    [hs-422_sws.SLDPRT, hs-422_sws.STEP]
2019-01-16 CAD du robot pour la patte
    Lachez pas
    [Assem2.SLDASM, Boutte_Servo.SLDPRT, Modäle_servomoteur.SLDPRT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]
2019-01-22 CAD des cartes
    [OpenC_dimensions.SLDPRT]
2019-01-23 Travail avant midi 23/01/19
    Vérification modèle du bras
    [ArduinoUNO.SLDPRT, Bras 1.SLDPRT, Part1.SLDPRT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]
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2019-01-23 ajout ébauches bras
    [Bras 1.SLDPRT, Bras 2.SLDPRT, Robotic.SLDASM]
2019-01-23 CAD base-support carte 23 janvier
    [base_v3-bas.SLDPRT, base_v3-top.SLDPRT, support_carte.SLDPRT]
2019-01-23 Support à patte Version 1
    Support à patte Version 1
    [Assemblage1.SLDASM, Base.SLDPRT, Connecteur_servo_moteur.SLDPRT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]
2019-01-23 Bras 2 fait, ébauche bras 1
    [Bras 1.SLDPRT, Bras 2.SLDPRT]
2019-01-23 Assemblage robot + Assemblage base + Support Cartes Ajustements
    Travail du 23 janvier 2019
    [Assemblage_de_la_base.SLDASM, Assemblage_du_robot.SLDASM, hs-422_sws.SLDPRT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]
2019-01-23 Bleu et vert fini, v1
    [Bleu 2.SLDPRT, Bras 1.SLDPRT, Vert.SLDPRT]
2019-01-23 Travail sur CAD de la base
    [PCA9685.SLDPRT]
2019-01-23 Support à patte version 2
    [Assemblage1.SLDASM, Base.SLDPRT, Bleu 2.SLDPRT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]
2019-01-24 Changement de couleur bras
    [Bleu 1.SLDPRT, Bleu 2.SLDPRT, Bleu 3.SLDPRT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]
2019-01-28 Ajout de fichier sldwrk test pour percage et spacer bas
    [SpacerCarteDuBas.SLDPRT, TestPercage_Bearing_unquart.SLDPRT, TestPercage_Bearing_unquart.STL]
2019-01-28 assemblage robot bon
    [Assemblage_du_robot.SLDASM]
2019-01-29 Ajout de tests et modifications suite a ces tests
    [Test_Trou_Cartes_Autres.SLDPRT, Test_Trou_Cartes_Autres.STL, base_v3-bas.SLDPRT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]
2019-01-29 update assemblage avec cover pour cartes
    [Assemblage1.SLDASM, Assemblage_du_robot.SLDASM, assemblage_support_carte_et_cover.SLDASM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]
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2019-01-29 Pattes presque fini
    [Assemblage1.SLDASM, Base.SLDPRT, Bleu 2.SLDPRT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]
2019-01-30 Modification du spacer du bas pour la base
    [SpacerCarteDuBas.SLDPRT, SpacerCarteDuBas.STL]
2019-01-30 robot tourné doit commit avant de pull
    [Assemblage_du_robot.SLDASM, assemblage_support_carte_et_cover.SLDASM]
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2019-01-30 Modification grosseur patte
    [Assemblage1.SLDASM, Assemblage_du_robot.SLDASM, Bleu1.SLDPRT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]
2019-01-30 Revert "Modification grosseur patte"
    This reverts commit 1dc17d099cf739cb7ef65c6194d3b937ae720d23.
    [Assemblage1.SLDASM, Assemblage_du_robot.SLDASM, Bleu1.SLDPRT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]
2019-01-30 Beau support de cartes
    [Test_Trou_Cartes_Autres.SLDPRT, cover carte.SLDPRT, support_carte.SLDPRT]
2019-01-30 Modif bras
    [Assemblage1.SLDASM]
2019-01-30 Vrai Modif Bras
    [Assemblage1.SLDASM, Bleu1.SLDPRT, Bleu2.0.SLDPRT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]
2019-01-30 Test percage vis
    [Assemblage_du_robot.SLDASM, Test_Percage_tite_vis.SLDPRT, Test_Percage_tite_vis.STL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]
2019-01-30 Modification trou de patte
    [Assemblage1.SLDASM, Base.SLDPRT, Bleu1.SLDPRT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]
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2019-01-30 will 30 janvier only commit
    [535198.STEP, 615398 assembly.SLDASM, Assemblage_du_robot.SLDASM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]
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2019-01-30 Changement du cover
    [cover-carte.SLDPRT]
2019-01-30 Changement cover 2.0
    [cover carte.SLDPRT, cover-carte.SLDPRT]
2019-01-30 push pour krill
    [assemblage_base_top.SLDASM]
2019-01-30 assemblage robot beau genre vrm magnifique
    [Assemblage1.SLDASM, base_v3-top.SLDPRT]
2019-02-05 Travail pour imprimer
    [Assemblage1.SLDASM, Assemblage_du_robot.SLDASM, Base.SLDPRT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]
2019-02-05 Updated Patte
    [Assemblage1.SLDASM]
2019-02-06 Derniere modif
    [Assemblage1.SLDASM, Base2.SLDPRT, Base2.STL]
2019-02-06 modif erreur base
    [base_v3-top-good.SLDPRT]
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2019-02-06 Modification de patte
    modification de la patte suite au premier assemblage
    [Assemblage1.SLDASM, Base2.SLDPRT, Bleu1.SLDPRT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]
2019-02-06 Modification patte 2
    Autres modifications pour sur la patte
    [Assemblage1.SLDASM, Bleu2.0.SLDPRT, Vert.SLDPRT]
2019-02-06 base robot avec glissiere pour moteurs
    [assemblage_base_top_glissiere.SLDASM, base_v3-top-glissiere.SLDPRT, glissiere_connexion_moteur.SLDPRT]
2019-02-06 Modification trou patte et STL
    [Assemblage1.SLDASM, Bleu1.SLDPRT, Bleu1.STL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]
2019-02-06 Modif joint B R
    [Assemblage1.SLDASM, Joint R-B.SLDPRT]
2019-02-06 Modification rouge 3
    [Assemblage1.SLDASM, Joint R-B.SLDPRT, Joint R-B.STL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]
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2019-02-14 Assemblages et STL
    [Assemblage1.SLDASM, Bleu2.0.SLDPRT, Bleu2.0.STL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]
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2019-02-18 Update cad robot
    [Assemblage1.SLDASM, Base.STL, Base2.STL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]
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2019-02-20 Travail Solidworks Avant CleanUp
    [Cinematique_Directe_Analytique.xlsx, Esquisse_Cinematique.SLDPRT]
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2019-03-10 CodeCinématiquePatte_v0
    Inclue la création de la cinématique d'une patte dans Matlab et le code Motion Genesis pour la cinématique
    [EsquisseBleu.SLDPRT, Esquisse_Cinematique.SLDPRT]
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2019-03-13 Modification cad patte 1
    [Patte.SLDASM, Spacer pour servo moteur.SLDPRT, WASHER.SLDPRT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]
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2019-03-27 Nouvelle copie (semaine du 25 mars): bug à valider avec équipe professoral
    [Cinematique.cpp, matrix.cpp, testCalculCinematic.ino]
2019-03-27 Bonne fonctions matlab: 1 a verifier
    [Qb_a_qbx.xlsx]
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2019-03-27 Revert "modif cad 2"
    This reverts commit 1f86cb7408a4530803a66092efef03fe0a1c1004.
    [Base.SLDASM, Patte.SLDASM, Tripod.SLDASM]
2019-03-27 Revert "Revert "modif cad 2""
    This reverts commit d4a5a5e44cf9b070f37916b02328cecc9bb00146.
    [Base.SLDASM, Patte.SLDASM, Tripod.SLDASM]
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2019-04-09 Essaie de faire fonctionner sur OpenCR -> fail
    [CalculCinematiqueOBJ.ino, ObjCinematique.h]
2019-04-10 Mise a jour plan
    [Base.SLDASM, Patte.SLDDRW, Tripod.SLDASM]
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
